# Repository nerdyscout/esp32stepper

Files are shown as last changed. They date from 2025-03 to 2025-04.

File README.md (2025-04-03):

# ESP32STEPPER

current state: untested :warning:

inspired by [joshr120/PD-Stepper](https://github.com/joshr120/PD-Stepper) but being fully open hardware/software.

Stepper motor controller using silent Trinamic TMC2209, ESP32-S3 and USB-PD mountable onto any NEMA17 motor. 

## Main Features:
- **TMC2209** stepper motor driver
- **ESP32-S3**
  - alternatively NE555 pulse generator
- **USB Power Delivery** providing up to 20V operation
  - alternatively external voltage supply possible
- **MPU-6050** 6axis accelerometer
- **BME280** temperature sensor
- **QWIIC** connector for external I2C components
- 2x **WS2812** RGB LEDs
- 2x **Push Buttons**
- optional 0.96" 128x96 **LC-Display**
- **JTAG** pins accessible
- **3 GPIO** pins and **UART** available

## PCB - License CERN-OHL-P-2.0

### Schematic

schematic

### Bill of Materials

The complete BOM is available in different formats:
  - raw [HTML](pcb/docs/bom/esp32stepper-bom.html)
  - interactive [HTML](nerdyscout.github.io/esp32stepper)
  - [CSV](pcb/docs/bom/esp32stepper-bom_octopart.csv) compliant to octopart

### Layout

| Top | Bottom |
| --- | --- |
| top view | bottom view |

### Gerbers

All fabrication files needed to produce this PCB are located within the [release package](https://github.com/nerdyscout/esp32stepper/releases).

## Mechanics

in the folder `cad` the spacers between motor and PCB, as well as the housing, can be found. One of the two spacer parts can be made out of metal to act as heatsink for the TMC2209. 

## Firmware

### ESPHome

There is a [esphome](https://esphome.io/) config file supporting different features located at `firmware/esphome`

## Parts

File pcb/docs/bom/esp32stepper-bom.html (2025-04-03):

Source File | esp32stepper.kicad_sch
BoM Date | Date
Schematic Version | 1.0
Schematic Date | 2025-03-16
PCB Variant | default
KiCad Version | Eeschema 9.0.1
Component Groups | 51
Component Count (per PCB) | 80
Fitted Components (per PCB) | 65
Number of PCBs | 1
Total Component Count (for 1 PCBs) | 65
 | Description | Part | References | Value | Footprint | Quantity Per PCB | Datasheet | variant | lcsc | sim.device | sim.pins | prod_id
1 | Unpolarized capacitor | C | C8C17C20C21C22C24 | 100nF | C_0402_1005Metric_Pad0.74x0.62mm_HandSolder | 6 | ~ | MPU | C7432762
2 | Unpolarized capacitor | C | C2C4C11C19 | 1µF | C_0402_1005Metric_Pad0.74x0.62mm_HandSolder | 4 | ~ | ESP32 USBPD | C14445
3 | Unpolarized capacitor | C | C14C15 | 10µF | C_0402_1005Metric_Pad0.74x0.62mm_HandSolder | 2 | ~ |  | C5252392
4 | Unpolarized capacitor | C | C3 | 10uF | C_0603_1608Metric_Pad1.08x0.95mm_HandSolder | 1 | ~ |  | C22367827
5 | Unpolarized capacitor | C | C13 | 100nF 16V | C_0402_1005Metric_Pad0.74x0.62mm_HandSolder | 1 | ~ |  | C7432762
6 | Unpolarized capacitor | C | C5C18 | 100nF 35V | C_0603_1608Metric_Pad1.08x0.95mm_HandSolder | 2 | ~ |  | C5342943
7 | Polarized capacitor | C_Polarized | C16 | 100µF 35V | C_Elec_6.3x7.7 | 1 | ~ |  | C4747966
8 | Unpolarized capacitor | C | C12 | 10µF 35V | C_0603_1608Metric_Pad1.08x0.95mm_HandSolder | 1 | ~ |  | C22367827
9 | Unpolarized capacitor | C | C7C9C10 | 1µF 35V | C_0603_1608Metric_Pad1.08x0.95mm_HandSolder | 3 | ~ |  | C7432774
10 | Unpolarized capacitor | C | C23 | 2,2nF 50V | C_0603_1608Metric_Pad1.08x0.95mm_HandSolder | 1 | ~ | MPU | C5119310
11 | Unpolarized capacitor | C | C6 | 22nF 50V | C_0603_1608Metric_Pad1.08x0.95mm_HandSolder | 1 | ~ |  | C915842
12 | Diode | D | D3 | D | D_SOD-123 | 1 | ~ | FAN | C95872 | D | 1=K 2=A
13 | RGB LED with integrated controller, 2.0 x 2.0 mm, 12 mA | WS2812B-2020 | D1D2 | WS2812B-2020 | LED_WS2812B-2020_PLCC4_2.0x2.0mm | 2 | https://cdn-shop.adafruit.com/product-files/4684/4684_WS2812B-2020_V1.3_EN.pdf | ESP32 | C965555
14 | Generic connector, single row, 01x07, script generated (kicad-library-utils/schlib/autogen/connector/) | Conn_01x07 | J1 | IO | JST_SH_SM07B-SRSS-TB_1x07-1MP_P1.00mm_Horizontal | 1 | https://www.jst-mfg.com/product/pdf/eng/eSH.pdf |  | C160406
15 | 4 pin JST 1mm polarized connector for I2C | Qwiic_Vertical | J4 | Qwiic_Vertical | JST_SH_SM04B-SRSS-TB_1x04-1MP_P1.00mm_Horizontal | 1 | https://www.jst-mfg.com/product/pdf/eng/eSH.pdf |  | C160404 |  |  | CONN-14483
16 | Generic connector, single row, 01x04, script generated (kicad-library-utils/schlib/autogen/connector/) | Conn_01x04 | J5 | Stepper | JST_PH_S4B-PH-K_1x04_P2.00mm_Horizontal | 1 | ~ |  | C19271361
17 | USB 2.0-only 14P Type-C Receptacle connector | USB_C_Receptacle_USB2.0_14P | J9 | USB_C_Receptacle_USB2.0_14P | USB_C_Receptacle_G-Switch_GT-USB-7010ASV | 1 | https://www.usb.org/sites/default/files/documents/usb_type-c.zip | USBPD | C2988369
18 | Inductor | L | L1 | 4,7µH | L_Bourns-SRN4018 | 1 | ~ |  | C1330726
19 | -3.6A Id, -30V Vds, 64mOhm Rds, P-Channel HEXFET Power MOSFET, SOT-23 | IRLML9301 | Q1Q2 | IRLML9301 | SOT-23 | 2 | https://www.infineon.com/dgdl/irlml9301pbf.pdf?fileId=5546d462533600a401535668e5e42640 | FAN | C7472922
20 | Resistor | R | R3R11 | 100m | R_0805_2012Metric_Pad1.20x1.40mm_HandSolder | 2 | ~ |  | C723643
21 | Resistor | R | R14 | 30 | R_0402_1005Metric_Pad0.72x0.64mm_HandSolder | 1 | ~ |  | C965208
22 | Resistor | R | R18 | 1k | R_0402_1005Metric_Pad0.72x0.64mm_HandSolder | 1 | ~ | USBPD | C2077651
23 | Resistor | R | R5 | 2k7 | R_0402_1005Metric_Pad0.72x0.64mm_HandSolder | 1 | ~ | ESP32 | C203149
24 | Resistor | R | R1R12R21 | 4k7 | R_0402_1005Metric_Pad0.72x0.64mm_HandSolder | 3 | ~ | ESP32 | C159885
25 | Resistor | R | R6R7R8R10R13R15R16R17R20R26 | 10k | R_0402_1005Metric_Pad0.72x0.64mm_HandSolder | 10 | ~ | ESP32 USBPD FAN | C304153
26 | Resistor | R | R2R4 | 20k | R_0402_1005Metric_Pad0.72x0.64mm_HandSolder | 2 | ~ | ESP32 | C93942
27 | Resistor | R | R9 | 33k | R_0402_1005Metric_Pad0.72x0.64mm_HandSolder | 1 | ~ |  | C427218
28 | Potentiometer | R_Potentiometer | RV1 | Potentiometer | Potentiometer_Bourns_TC33X_Vertical | 1 | ~ |  | C720648
29 | Microminiature SMT Side Actuated, 4.2 x 2.8 x 1.42mm, without pegs, with shield pin | CK_KMS2xxG | SW3 | B1 | SW_SPST_CK_KMS2xxGP | 1 | https://www.ckswitches.com/media/1482/kms.pdf | ESP32 | C221703
30 | Microminiature SMT Side Actuated, 4.2 x 2.8 x 1.42mm, without pegs, with shield pin | CK_KMS2xxG | SW4 | B2 | SW_SPST_CK_KMS2xxGP | 1 | https://www.ckswitches.com/media/1482/kms.pdf | ESP32 | C221703
31 | Microminiature SMT Side Actuated, 4.2 x 2.8 x 1.42mm, without pegs, with shield pin | CK_KMS2xxG | SW1 | BOOT | SW_SPST_CK_KMS2xxGP | 1 | https://www.ckswitches.com/media/1482/kms.pdf | ESP32 | C221703
32 | Microminiature SMT Side Actuated, 4.2 x 2.8 x 1.42mm, without pegs, with shield pin | CK_KMS2xxG | SW2 | RST | SW_SPST_CK_KMS2xxGP | 1 | https://www.ckswitches.com/media/1482/kms.pdf | ESP32 | C221703
33 | 3-in-1 sensor, humidity, pressure, temperature, I2C and SPI interface, 1.71-3.6V, LGA-8 | BME280 | U3 | BME280 | Bosch_LGA-8_2.5x2.5mm_P0.65mm_ClockwisePinNumbering | 1 | https://www.bosch-sensortec.com/media/boschsensortec/downloads/datasheets/bst-bme280-ds002.pdf | ESP32 | C92489
34 | 100W USB Type-C PD3.0/2.0, BC1.2 Sink Controller, SSOP-10 | CH224K | U6 | CH224K | SSOP-10-1EP_3.9x4.9mm_P1mm_EP2.1x3.3mm | 1 | https://www.wch.cn/downloads/file/301.html | USB | C970725
35 | Smallsized module supporting 2.4 GHz WiFi (802.11 b/g/n) and Bluetooth ® 5 (LE) Built around ESP32S3 series of SoCs, Xtensa ® dualcore 32bit LX7 microprocessor Flash up to 8 MB, optional 2 MB PSRAM in chip package 39 GPIOs, rich set of peripherals Onboard PCB antenna or external antenna connector | ESP32-S3-MINI-1 | U4 | ESP32-S3-MINI-1 | ESP32-S3-MINI-1 | 1 | https://www.espressif.com/sites/default/files/documentation/esp32-s3-mini-1_mini-1u_datasheet_en.pdf | ESP32 | C2913206
36 | InvenSense 6-Axis Motion Sensor, Gyroscope, Accelerometer, I2C | MPU-6050 | U7 | MPU-6050 | InvenSense_QFN-24_4x4mm_P0.5mm | 1 | https://invensense.tdk.com/wp-content/uploads/2015/02/MPU-6000-Datasheet1.pdf | MPU | C24112
37 | Standalone driver for two-phase bipolar stepper motor, 2A, 4.75… 36V, UART, internal FETs, QFN28 | TMC2208-LA | U2 | TMC2208-LA | QFN-28-1EP_5x5mm_P0.5mm_EP3.1x3.1mm_ThermalVias | 1 | https://www.analog.com/media/en/technical-documentation/data-sheets/TMC2202_TMC2208_TMC2224_datasheet_rev1.13.pdf |  | C115944
38 | 4.5V to 24V Input, 3-A Output Synchronous Buck Converter, SOT-23-6 | TPS56339DDC | U5 | TPS56339DDC | SOT-23-6 | 1 | https://www.ti.com/lit/ds/symlink/tps56339.pdf |  | C2071106
 | Description | Part | References | Value | Footprint | Quantity Per PCB | Datasheet | variant | lcsc | sim.device | sim.pins | prod_id
1 | Unpolarized capacitor | C | C1 | 100nF | C_0402_1005Metric_Pad0.74x0.62mm_HandSolder | 1 (DNF) | ~ | NE555
2 | Unpolarized capacitor | C | C25 | 1µF | C_0603_1608Metric_Pad1.08x0.95mm_HandSolder | 1 (DNF) | ~ | NE555
3 | Generic connector, single row, 01x04, script generated (kicad-library-utils/schlib/autogen/connector/) | Conn_01x04 | J3 | Display 0.96" 128x96 | PinSocket_1x04_P2.54mm_Vertical | 1 (DNF) | ~
4 | Generic connector, single row, 01x03, script generated (kicad-library-utils/schlib/autogen/connector/) | Conn_01x03 | J8 | FAN | Harwin_M20-89003xx_1x03_P2.54mm_Horizontal | 1 (DNF) | ~
5 | Cortex Debug Connector, standard ARM Cortex-M SWD and JTAG interface | Conn_ARM_JTAG_SWD_10 | J7 | JTAG | PinHeader_2x05_P1.27mm_Vertical_SMD | 1 (DNF) | http://infocenter.arm.com/help/topic/com.arm.doc.ddi0314h/DDI0314H_coresight_components_trm.pdf
6 | 2 Pin 2mm JST Battery Connector | Conn_01x02_JST_2.0mm_LiPo | J6 | PWR | JST_SMD_2.0mm-2 | 1 (DNF) | ~ |  |  |  |  | CONN-11443
7 | Solder Jumper, 2-pole, open | SolderJumper_2_Open | JP3 | MS1 | SolderJumper-2_P1.3mm_Open_RoundedPad1.0x1.5mm | 1 (DNF) | ~
8 | Solder Jumper, 2-pole, open | SolderJumper_2_Open | JP4 | MS2 | SolderJumper-2_P1.3mm_Open_RoundedPad1.0x1.5mm | 1 (DNF) | ~
9 | Resistor | R | R24 | 1k | R_0402_1005Metric_Pad0.72x0.64mm_HandSolder | 1 (DNF) | ~ | NE555
10 | Resistor | R | R19R22R25 | 10k | R_0402_1005Metric_Pad0.72x0.64mm_HandSolder | 3 (DNF) | ~ | USBPD NE555 | C304153
11 | Resistor | R | R23 | 20k | R_0402_1005Metric_Pad0.72x0.64mm_HandSolder | 1 (DNF) | ~ | NE555
12 | Rotary encoder, dual channel, incremental quadrate outputs | RotaryEncoder | SW5 | RotaryEncoder |  | 1 (DNF) | ~
13 | Precision Timers, 555 compatible, VSSOP-8 | LM555xMM | U1 | LM555xMM | VSSOP-8_3x3mm_P0.65mm | 1 (DNF) | http://www.ti.com/lit/ds/symlink/lm555.pdf | NE555

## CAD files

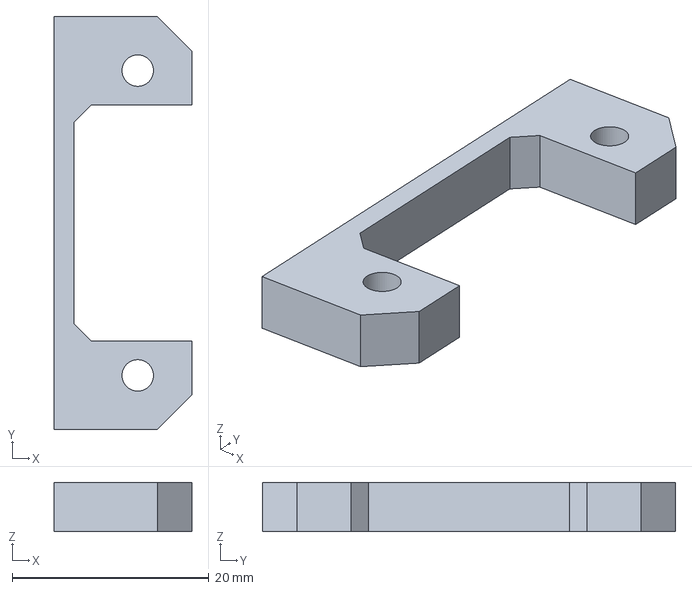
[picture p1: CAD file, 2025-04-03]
cad/plastic.step
14.0 x 42.0 x 5.00 mm

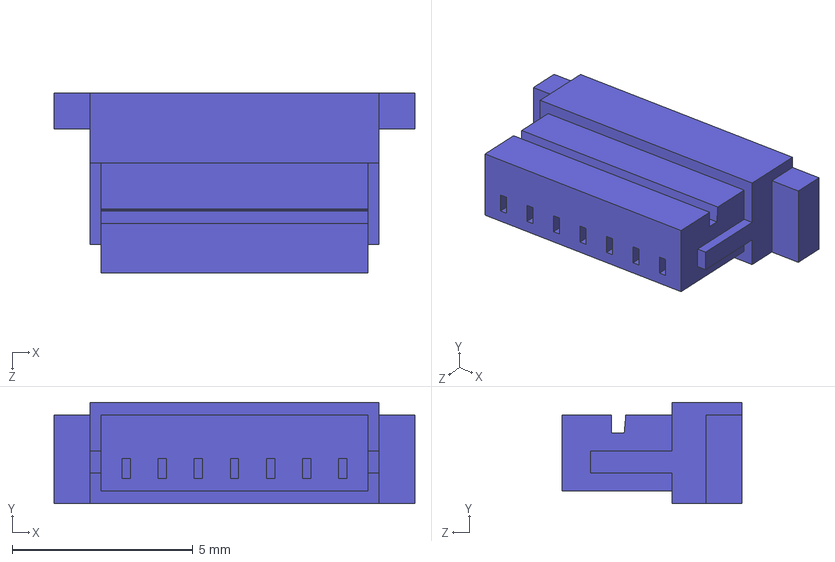
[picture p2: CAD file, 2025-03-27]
pcb/3dmodels/SHR-07V-S-B.step
10.0 x 2.80 x 5.00 mm

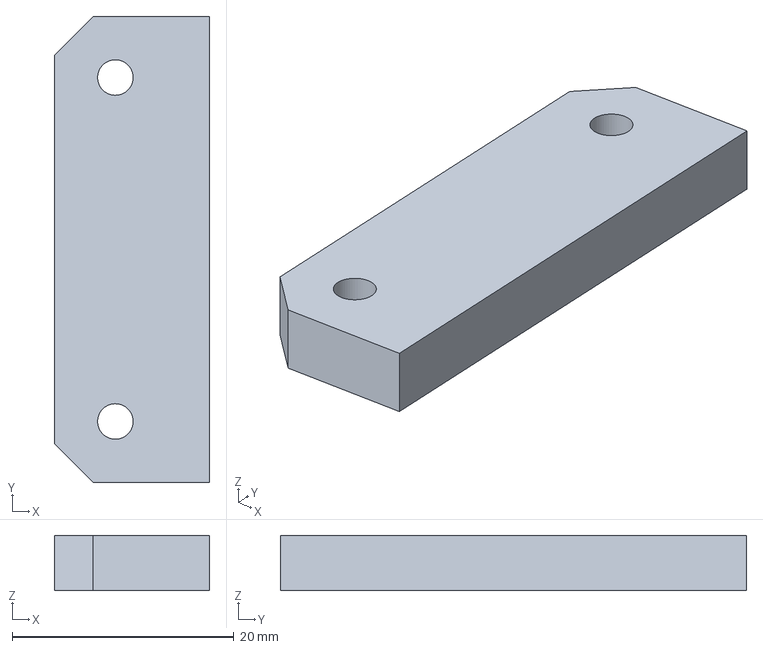
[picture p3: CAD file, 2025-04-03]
cad/metal.step
14.0 x 42.0 x 5.00 mm

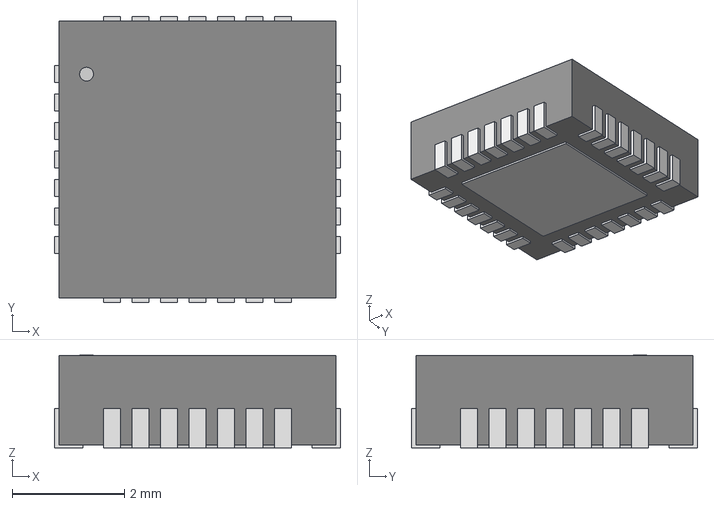
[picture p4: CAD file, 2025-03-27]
pcb/3dmodels/QFN28_5X5MC_MCH.step
5.11 x 5.11 x 1.65 mm

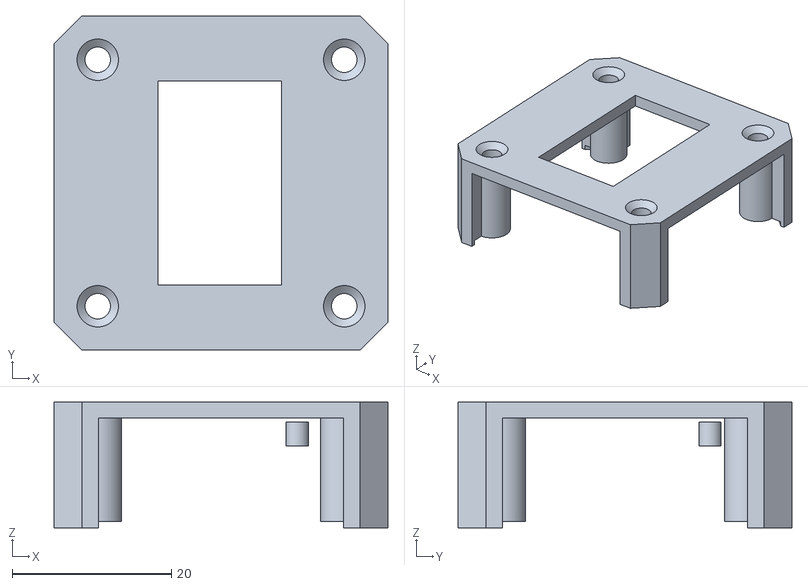
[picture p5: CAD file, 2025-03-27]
cad/cover_with_lcd.stl
42.0 x 42.0 x 15.8

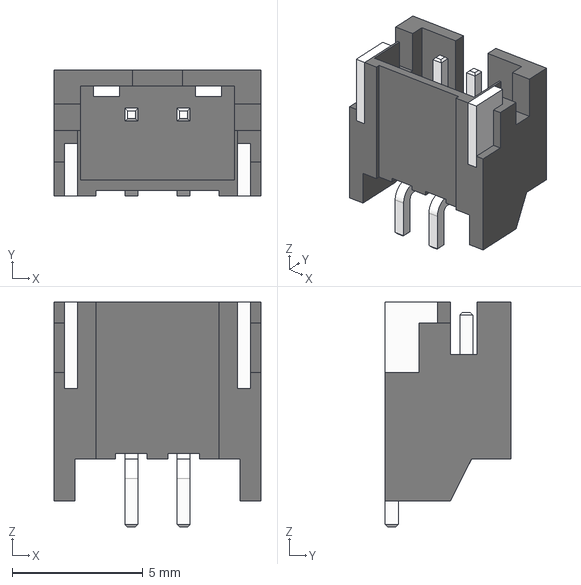
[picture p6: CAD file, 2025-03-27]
pcb/3dmodels/JST-PH-2 v1.step
7.90 x 4.80 x 8.60 mm

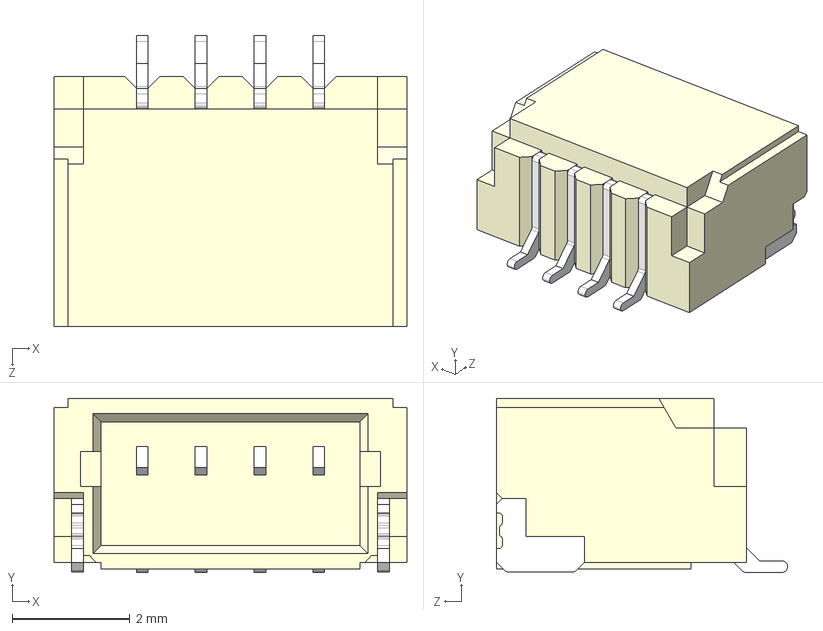
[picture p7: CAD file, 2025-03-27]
pcb/3dmodels/SM04B-SRSS-TB.step
6.00 x 2.96 x 4.95 mm

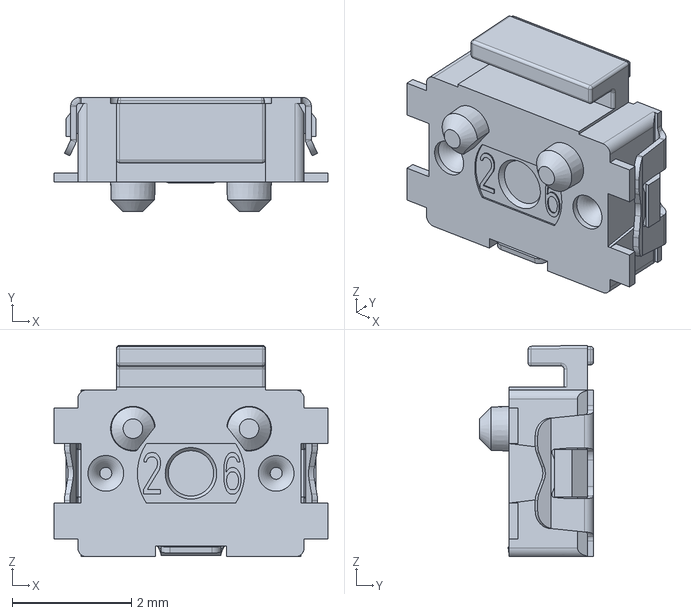
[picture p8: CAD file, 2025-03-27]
pcb/3dmodels/KMS221GPLFS.step
4.60 x 1.92 x 3.55 mm

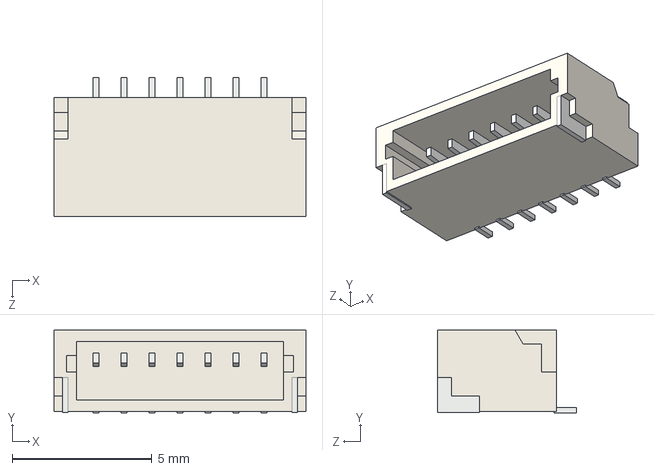
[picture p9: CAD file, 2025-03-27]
pcb/3dmodels/JST SM07B-SRSS-TB.step
9.00 x 2.96 x 4.95 mm

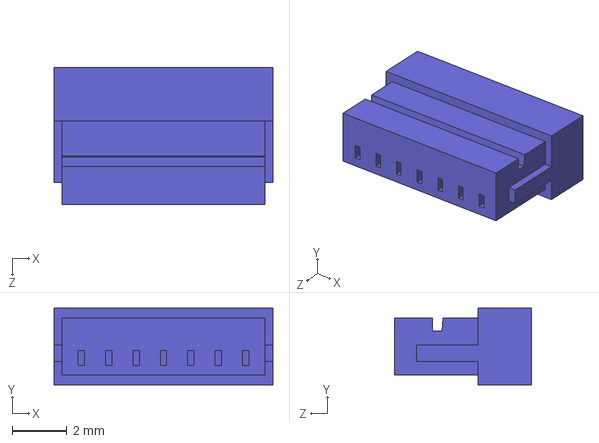
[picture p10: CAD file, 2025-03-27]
pcb/3dmodels/SHR-07V-S.step
8.00 x 2.80 x 5.00 mm

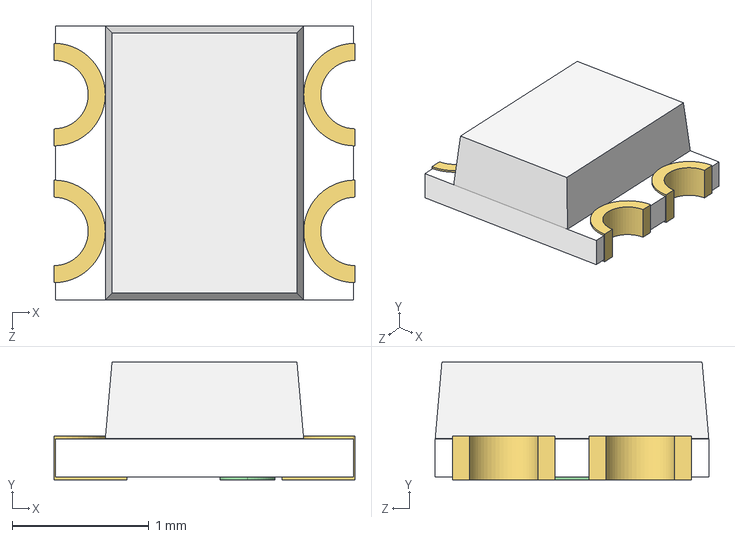
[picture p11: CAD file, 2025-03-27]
pcb/3dmodels/WS2812-2020.step
2.20 x 0.86 x 2.00 mm

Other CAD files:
cad/metal.stl
cad/plastic.stl

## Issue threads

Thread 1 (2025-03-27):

tasks left to do

nerdyscout, 2025-03-27:
* [ ] add option to use AS5600
 * [ ] check if magnetic sensor can detect rotation, distance piece might be to tall
 * [ ] improve documentation
 * [ ] make sure pnp file fits jlcpcb
 * [ ] add OSHWA id to pcb once granted

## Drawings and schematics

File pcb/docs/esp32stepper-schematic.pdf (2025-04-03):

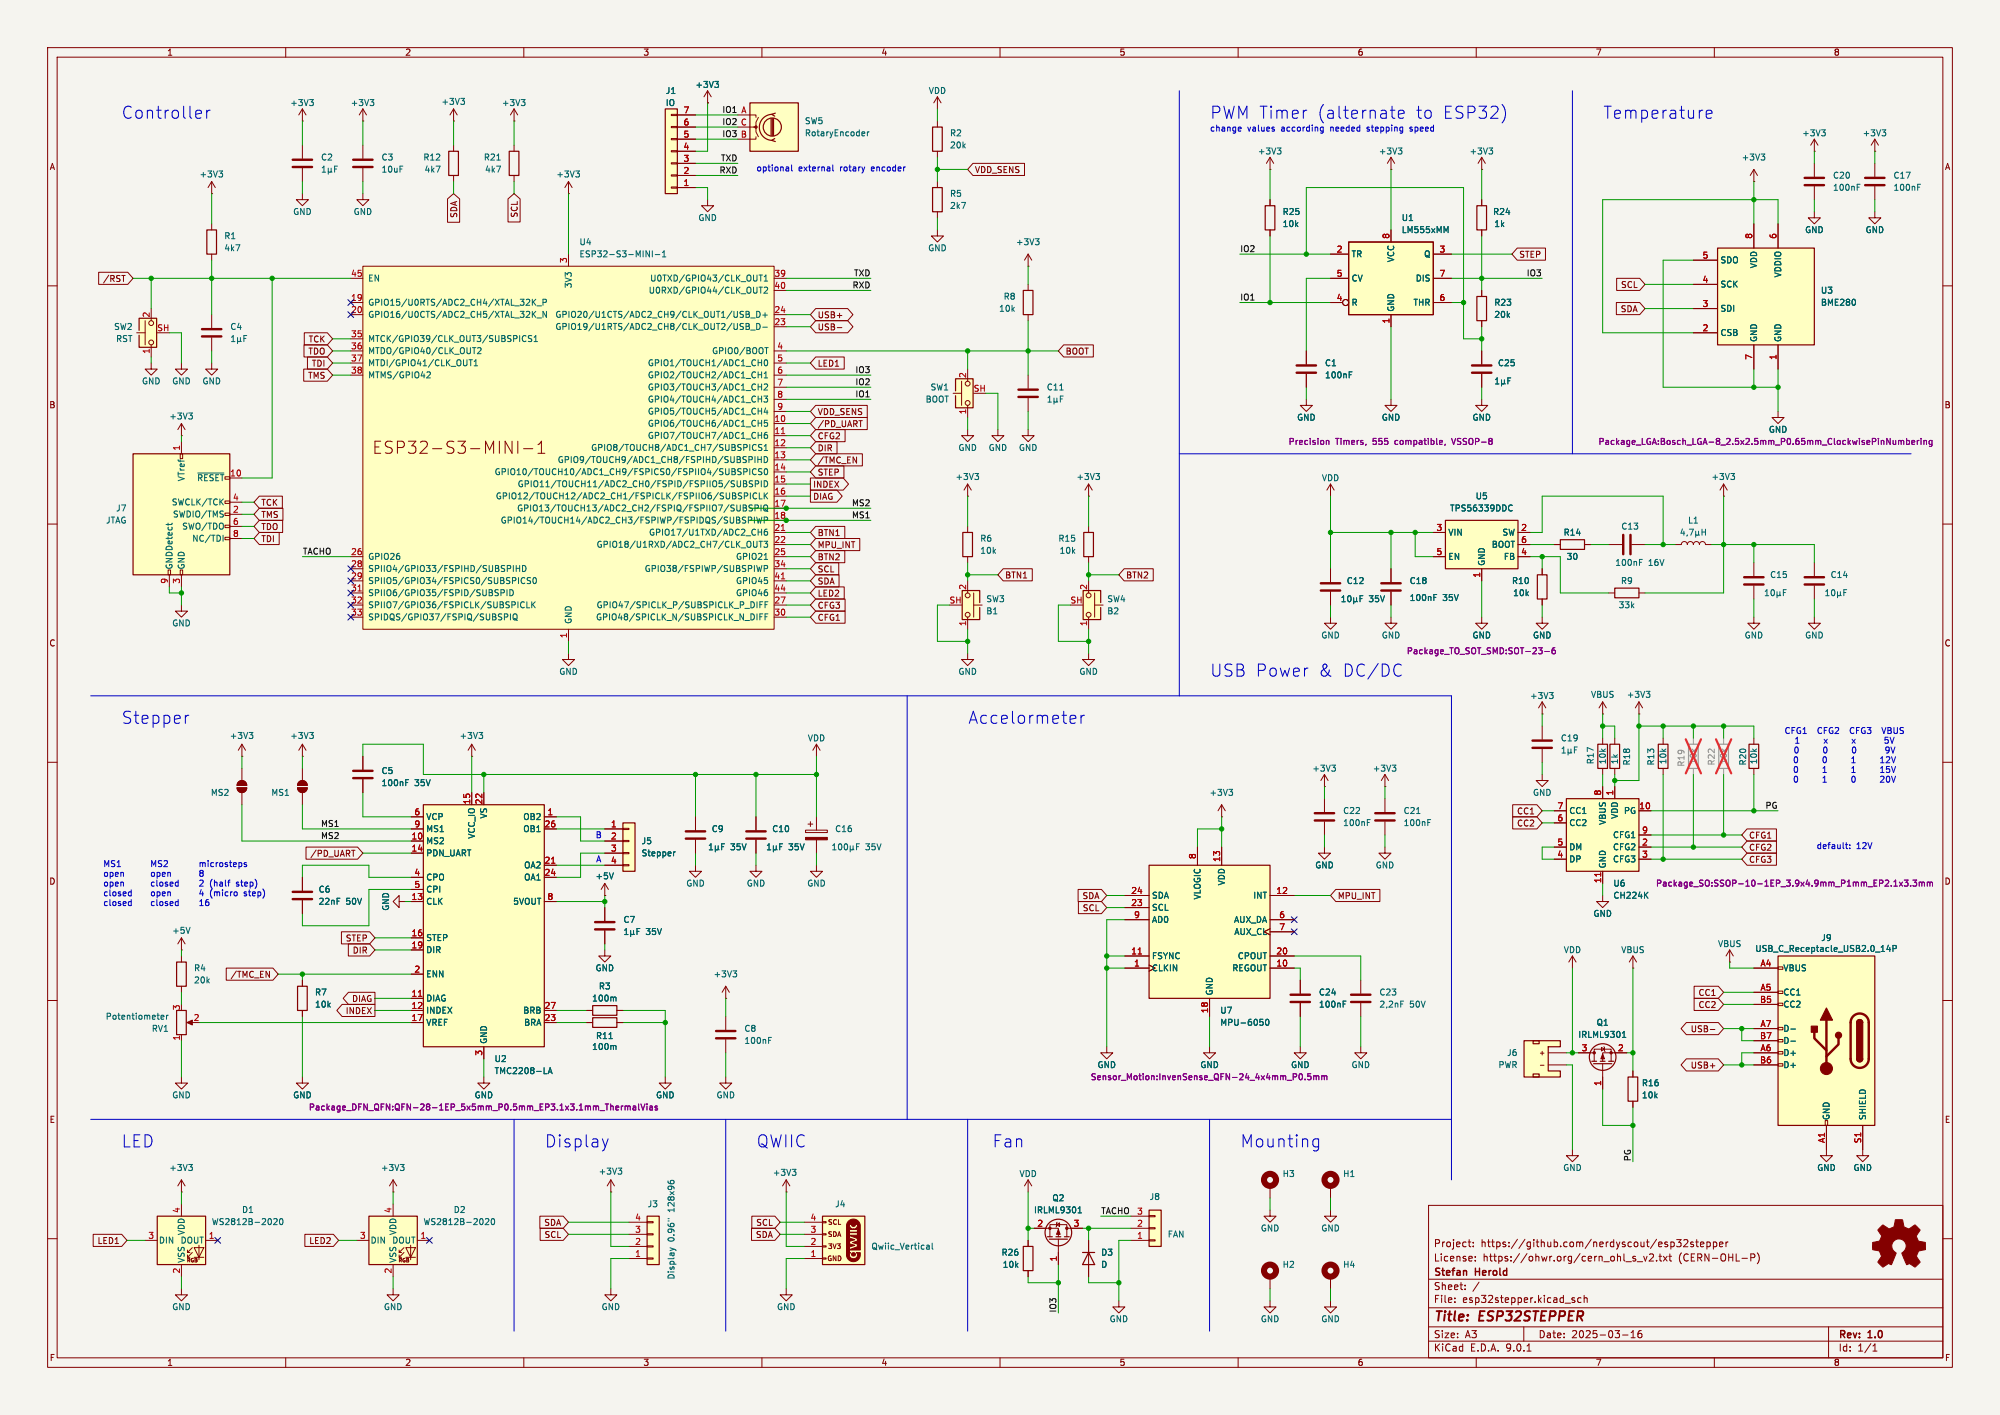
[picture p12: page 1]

1 U0TXD/GPIO43/CLK_OUT1 39 U0RXD/GPIO44/CLK_OUT2 40 GPIO20/U1CTS/ADC2_CH9/CLK_OUT1/USB_D+ 24 GPIO19/U1RTS/ADC2_CH8/CLK_OUT2/USB_D- 23 GPIO0/BOOT 4 GPIO1/TOUCH1/ADC1_CH0 5 GPIO2/TOUCH2/ADC1_CH1 6 GPIO3/TOUCH3/ADC1_CH2 7 GPIO4/TOUCH4/ADC1_CH3 8 GPIO5/TOUCH5/ADC1_CH4 9 GPIO6/TOUCH6/ADC1_CH5 10 GPIO7/TOUCH7/ADC1_CH6 11 GPIO8/TOUCH8/ADC1_CH7/SUBSPICS1 12 GPIO9/TOUCH9/ADC1_CH8/FSPIHD/SUBSPIHD 13 GPIO10/TOUCH10/ADC1_CH9/FSPICS0/FSPIIO4/SUBSPICS0 14 GPIO11/TOUCH11/ADC2_CH0/FSPID/FSPIIO5/SUBSPID 15 GPIO12/TOUCH12/ADC2_CH1/FSPICLK/FSPIIO6/SUBSPICLK 16 GPIO13/TOUCH13/ADC2_CH2/FSPIQ/FSPIIO7/SUBSPIQ 17 GPIO14/TOUCH14/ADC2_CH3/FSPIWP/FSPIDQS/SUBSPIWP 18 GPIO17/U1TXD/ADC2_CH6 21 GPIO18/U1RXD/ADC2_CH7/CLK_OUT3 22 GPIO21 25 GPIO38/FSPIWP/SUBSPIWP 34 GPIO45 41 GPIO46 44 GPIO47/SPICLK_P/SUBSPICLK_P_DIFF 27 GPIO48/SPICLK_N/SUBSPICLK_N_DIFF 30 U4ESP32-S3-MINI-1 +3V3

þÿ1µF GND GND GND

3 ~{RESET}10 SWCLK/TCK 4 SWDIO/TMS 2 SWO/TDO 6 NC/TDI 8

VCP 6 MS1 9 MS2 10 PDN_UART 14 CPO 4 CPI 5 CLK 13 STEP 16 DIR 19 ENN 2 DIAG 11

USB Power & DC/DC

Package_DFN_QFN:QFN-28-1EP_5x5mm_P0.5mm_EP3.1x3.1mm_ThermalVias VCP 6 MS1 9 MS2 10 PDN_UART 14 CPO 4 CPI 5 CLK 13 STEP 16 DIR 19 ENN 2 DIAG 11

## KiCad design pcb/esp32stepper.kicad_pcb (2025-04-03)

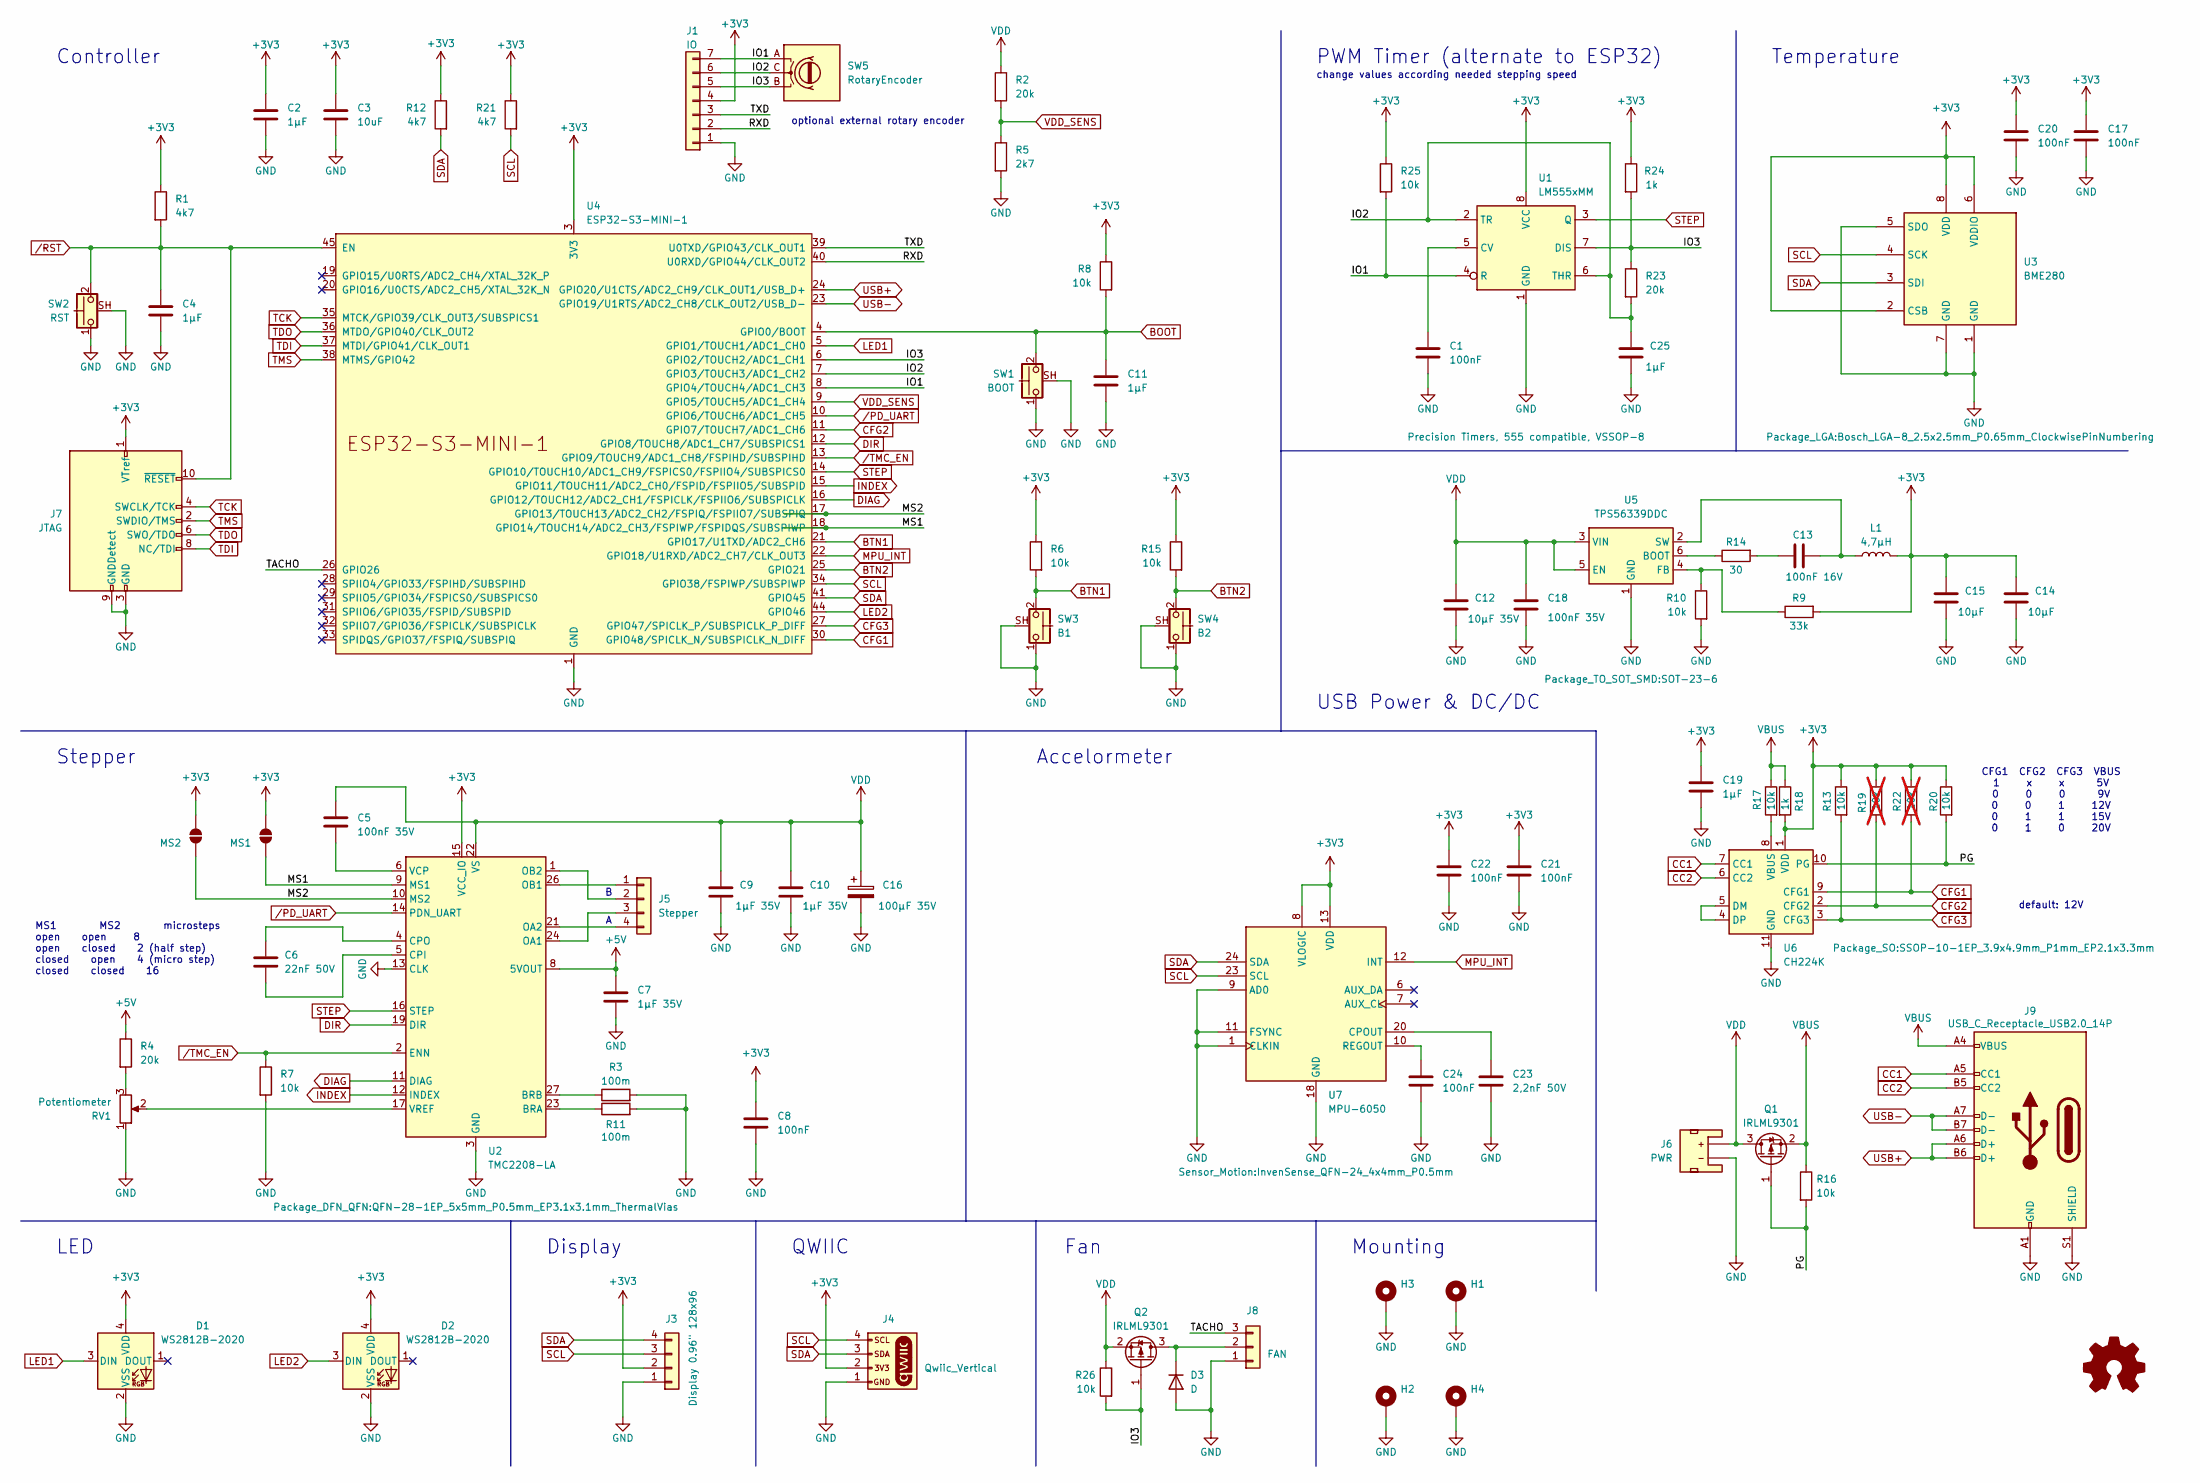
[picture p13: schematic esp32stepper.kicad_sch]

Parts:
C1: 100nF; C_0402_1005Metric_Pad0.74x0.62mm_HandSolder
C2, C4, C11, C19: 1µF; C_0402_1005Metric_Pad0.74x0.62mm_HandSolder; LCSC C14445
C3: 10uF; C_0603_1608Metric_Pad1.08x0.95mm_HandSolder; LCSC C22367827
C5, C18: 100nF 35V; C_0603_1608Metric_Pad1.08x0.95mm_HandSolder; LCSC C5342943
C6: 22nF 50V; C_0603_1608Metric_Pad1.08x0.95mm_HandSolder; LCSC C915842
C7, C9, C10: 1µF 35V; C_0603_1608Metric_Pad1.08x0.95mm_HandSolder; LCSC C7432774
C8, C17, C20, C21, C22, C24: 100nF; C_0402_1005Metric_Pad0.74x0.62mm_HandSolder; LCSC C7432762
C12: 10µF 35V; C_0603_1608Metric_Pad1.08x0.95mm_HandSolder; LCSC C22367827
C13: 100nF 16V; C_0402_1005Metric_Pad0.74x0.62mm_HandSolder; LCSC C7432762
C14, C15: 10µF; C_0402_1005Metric_Pad0.74x0.62mm_HandSolder; LCSC C5252392
C16: 100µF 35V; C_Elec_6.3x7.7; LCSC C4747966
C23: 2,2nF 50V; C_0603_1608Metric_Pad1.08x0.95mm_HandSolder; LCSC C5119310
C25: 1µF; C_0603_1608Metric_Pad1.08x0.95mm_HandSolder
D1, D2: WS2812B-2020; LED_WS2812B-2020_PLCC4_2.0x2.0mm; LCSC C965555
D3: D; D_SOD-123; LCSC C95872
H1, H2, H3, H4: MountingHole_Pad; MountingHole_3.2mm_M3_Pad_Via
J1: IO; JST_SH_SM07B-SRSS-TB_1x07-1MP_P1.00mm_Horizontal; LCSC C160406
J3: Display 0.96" 128x96; PinSocket_1x04_P2.54mm_Vertical
J4: Qwiic_Vertical; JST_SH_SM04B-SRSS-TB_1x04-1MP_P1.00mm_Horizontal; LCSC C160404
J5: Stepper; JST_PH_S4B-PH-K_1x04_P2.00mm_Horizontal; LCSC C19271361
J6: PWR; JST_SMD_2.0mm-2
J7: JTAG; PinHeader_2x05_P1.27mm_Vertical_SMD
J8: FAN; Harwin_M20-89003xx_1x03_P2.54mm_Horizontal
J9: USB_C_Receptacle_USB2.0_14P; USB_C_Receptacle_G-Switch_GT-USB-7010ASV; LCSC C2988369
JP3: MS1; SolderJumper-2_P1.3mm_Open_RoundedPad1.0x1.5mm
JP4: MS2; SolderJumper-2_P1.3mm_Open_RoundedPad1.0x1.5mm
L1: 4,7µH; L_Bourns-SRN4018; LCSC C1330726
Q1, Q2: IRLML9301; SOT-23; LCSC C7472922
R1, R12, R21: 4k7; R_0402_1005Metric_Pad0.72x0.64mm_HandSolder; LCSC C159885
R2, R4: 20k; R_0402_1005Metric_Pad0.72x0.64mm_HandSolder; LCSC C93942
R3, R11: 100m; R_0805_2012Metric_Pad1.20x1.40mm_HandSolder; LCSC C723643
R5: 2k7; R_0402_1005Metric_Pad0.72x0.64mm_HandSolder; LCSC C203149
R6, R7, R8, R10, R13, R15, R16, R17, R20, R26: 10k; R_0402_1005Metric_Pad0.72x0.64mm_HandSolder; LCSC C304153
R9: 33k; R_0402_1005Metric_Pad0.72x0.64mm_HandSolder; LCSC C427218
R14: 30; R_0402_1005Metric_Pad0.72x0.64mm_HandSolder; LCSC C965208
R18: 1k; R_0402_1005Metric_Pad0.72x0.64mm_HandSolder; LCSC C2077651
R19, R22: 10k; R_0402_1005Metric_Pad0.72x0.64mm_HandSolder; LCSC C304153; not fitted
R23: 20k; R_0402_1005Metric_Pad0.72x0.64mm_HandSolder
R24: 1k; R_0402_1005Metric_Pad0.72x0.64mm_HandSolder
R25: 10k; R_0402_1005Metric_Pad0.72x0.64mm_HandSolder
RV1: Potentiometer; Potentiometer_Bourns_TC33X_Vertical; LCSC C720648
SW1: BOOT; SW_SPST_CK_KMS2xxGP; LCSC C221703
SW2: RST; SW_SPST_CK_KMS2xxGP; LCSC C221703
SW3: B1; SW_SPST_CK_KMS2xxGP; LCSC C221703
SW4: B2; SW_SPST_CK_KMS2xxGP; LCSC C221703
SW5: RotaryEncoder
U1: LM555xMM; VSSOP-8_3x3mm_P0.65mm
U2: TMC2208-LA; QFN-28-1EP_5x5mm_P0.5mm_EP3.1x3.1mm_ThermalVias; LCSC C115944
U3: BME280; Bosch_LGA-8_2.5x2.5mm_P0.65mm_ClockwisePinNumbering; LCSC C92489
U4: ESP32-S3-MINI-1; LCSC C2913206
U5: TPS56339DDC; SOT-23-6; LCSC C2071106
U6: CH224K; SSOP-10-1EP_3.9x4.9mm_P1mm_EP2.1x3.3mm; LCSC C970725
U7: MPU-6050; InvenSense_QFN-24_4x4mm_P0.5mm; LCSC C24112

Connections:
+3V3: C2.1, C3.1, C8.1, C14.1, C15.1, C17.1, C19.1, C20.1, C21.1, C22.1, D1.4 (VDD), D2.4 (VDD), J1.4, J3.2, J4.2, J7.1 (VTref), JP3.1 (A), JP4.1 (A), L1.2, R1.1, R6.1, R8.1, R9.2, R12.1, R13.1, R15.1, R18.2, R19.1, R20.1, R21.1, R22.1, R24.1, R25.1, U1.8 (VCC), U2.15 (VCC_IO), U3.2 (CSB), U3.6 (VDDIO), U3.8 (VDD), U4.3 (3V3), U6.1 (VDD), U7.8 (VLOGIC), U7.13 (VDD)
+5V: C7.1, R4.1, U2.8 (5VOUT)
/IO1: J1.7, R25.2, SW5.A, U1.4 (R), U4.8 (GPIO4/TOUCH4/ADC1_CH3)
/IO2: C25.1, J1.6, R23.2, SW5.C, U1.2 (TR), U1.6 (THR), U4.7 (GPIO3/TOUCH3/ADC1_CH2)
/IO3: J1.5, Q2.1 (G), R23.1, R24.2, R26.2, SW5.B, U1.7 (DIS), U4.6 (GPIO2/TOUCH2/ADC1_CH1)
/MS1: JP3.2 (B), U2.9 (MS1), U4.18 (GPIO14/TOUCH14/ADC2_CH3/FSPIWP/FSPIDQS/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)
/MS2: JP4.2 (B), U2.10 (MS2), U4.17 (GPIO13/TOUCH13/ADC2_CH2/FSPIQ/FSPIIO7/S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)
/PG: Q1.1 (G), R16.2, R20.2, U6.10 (PG)
/RXD: J1.2, U4.40 (U0RXD/GPIO44/CLK_OUT2)
/TACHO: J8.3, U4.26 (GPIO26)
/TXD: J1.3, U4.39 (U0TXD/GPIO43/CLK_OUT1)
BOOT: C11.1, R8.2, SW1.2, U4.4 (GPIO0/BOOT)
BTN1: R6.2, SW3.2, U4.21 (GPIO17/U1TXD/ADC2_CH6)
BTN2: R15.2, SW4.2, U4.25 (GPIO21)
CC1: J9.A5 (CC1), U6.7 (CC1)
CC2: J9.B5 (CC2), U6.6 (CC2)
CFG1: R22.2, U4.30 (GPIO48/SPICLK_N/SUBSPICLK_N_DIFF), U6.9 (CFG1)
CFG2: R19.2, U4.11 (GPIO7/TOUCH7/ADC1_CH6), U6.2 (CFG2)
CFG3: R13.2, U4.27 (GPIO47/SPICLK_P/SUBSPICLK_P_DIFF), U6.3 (CFG3)
DIAG: U2.11 (DIAG), U4.16 (GPIO12/TOUCH12/ADC2_CH1/FSPICLK/FSPIIO6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)
DIR: U2.19 (DIR), U4.12 (GPIO8/TOUCH8/ADC1_CH7/SUBSPICS1)
GND: C1.2, C2.2, C3.2, C4.2, C7.2, C8.2, C9.2, C10.2, C11.2, C12.2, C14.2, C15.2, C16.2, C17.2, C18.2, C19.2, C20.2, C21.2, C22.2, C23.2, C24.2, C25.2, D1.2 (VSS), D2.2 (VSS), D3.2 (A), H1.1, H2.1, H3.1, H4.1, J1.1, J3.1, J4.1, J6.1 (-), J7.3 (GND), J7.5 (GND), J7.9 (GNDDetect), J8.1, J9.A1 (GND), J9.A12 (GND), J9.B1 (GND), J9.B12 (GND), J9.S1 (SHIELD), R3.2, R5.2, R7.2, R10.2, R11.2, RV1.1, SW1.1, SW1.SH (B), SW2.1, SW2.SH (B), SW3.1, SW3.SH (B), SW4.1, SW4.SH (B), U1.1 (GND), U2.3 (GND), U2.13 (CLK), U2.18 (GND), U2.29 (GND), U3.1 (GND), U3.5 (SDO), U3.7 (GND), U4.1 (GND), U4.2 (GND), U4.42 (GND), U4.43 (GND), U4.46 (GND), U4.47 (GND), U4.48 (GND), U4.49 (GND), U4.50 (GND), U4.51 (GND), U4.52 (GND), U4.53 (GND), U4.54 (GND), U4.55 (GND), U4.56 (GND), U4.57 (GND), U4.58 (GND), U4.59 (GND), U4.60 (GND), U4.61 (GND), U4.62 (GND), U4.63 (GND), U4.64 (GND), U4.65 (GND), U5.1 (GND), U6.11 (GND), U7.1 (CLKIN), U7.9 (AD0), U7.11 (FSYNC), U7.18 (GND)
INDEX: U2.12 (INDEX), U4.15 (GPIO11/TOUCH11/ADC2_CH0/FSPID/FSPIIO5/S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)
LED1: D1.3 (DIN), U4.5 (GPIO1/TOUCH1/ADC1_CH0)
LED2: D2.3 (DIN), U4.44 (GPIO46)
MPU_INT: U4.22 (GPIO18/U1RXD/ADC2_CH7/CLK_OUT3), U7.12 (INT)
unnamed: C13.1, R14.2
unnamed: D3.1 (K), J8.2, Q2.3 (D)
unnamed: J5.1, U2.26 (OB1)
unnamed: J5.2, U2.1 (OB2)
unnamed: J5.3, U2.24 (OA1)
unnamed: J5.4, U2.21 (OA2)
unnamed: R4.2, RV1.3
unnamed: C1.1, U1.5 (CV)
unnamed: R11.1, U2.23 (BRA)
unnamed: R3.1, U2.27 (BRB)
unnamed: C6.2, U2.5 (CPI)
unnamed: C6.1, U2.4 (CPO)
unnamed: C5.2, U2.6 (VCP)
unnamed: RV1.2, U2.17 (VREF)
unnamed: R14.1, U5.6 (BOOT)
unnamed: R9.1, R10.1, U5.4 (FB)
unnamed: C13.2, L1.1, U5.2 (SW)
unnamed: U6.4 (DP), U6.5 (DM)
unnamed: R17.2, U6.8 (VBUS)
unnamed: C23.1, U7.20 (CPOUT)
unnamed: C24.1, U7.10 (REGOUT)
SCL: J3.3, J4.4, R21.2, U3.4 (SCK), U4.34 (GPIO38/FSPIWP/SUBSPIWP), U7.23 (SCL)
SDA: J3.4, J4.3, R12.2, U3.3 (SDI), U4.41 (GPIO45), U7.24 (SDA)
STEP: U1.3 (Q), U2.16 (STEP), U4.14 (GPIO10/TOUCH10/ADC1_CH9/FSPICS0/FSPIIO4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)
TCK: J7.4 (SWCLK/TCK), U4.35 (MTCK/GPIO39/CLK_OUT3/SUBSPICS1)
TDI: J7.8 (NC/TDI), U4.37 (MTDI/GPIO41/CLK_OUT1)
TDO: J7.6 (SWO/TDO), U4.36 (MTDO/GPIO40/CLK_OUT2)
TMS: J7.2 (SWDIO/TMS), U4.38 (MTMS/GPIO42)
USB+: J9.A6 (D+), J9.B6 (D+), U4.24 (GPIO20/U1CTS/ADC2_CH9/CLK_OUT1/USB_D+)
USB-: J9.A7 (D-), J9.B7 (D-), U4.23 (GPIO19/U1RTS/ADC2_CH8/CLK_OUT2/USB_D-)
VBUS: J9.A4 (VBUS), J9.A9 (VBUS), J9.B4 (VBUS), J9.B9 (VBUS), Q1.2 (S), R16.1, R17.1, R18.1
VDD: C5.1, C9.1, C10.1, C12.1, C16.1, C18.1, J6.2 (+), Q1.3 (D), Q2.2 (S), R2.1, R26.1, U2.22 (VS), U2.28 (VS), U5.3 (VIN), U5.5 (EN)
VDD_SENS: R2.2, R5.1, U4.9 (GPIO5/TOUCH5/ADC1_CH4)
/PD_UART: U2.14 (PDN_UART), U4.10 (GPIO6/TOUCH6/ADC1_CH5)
/RST: C4.1, J7.10 (~RESET), R1.2, SW2.2, U4.45 (EN)
/TMC_EN: R7.1, U2.2 (ENN), U4.13 (GPIO9/TOUCH9/ADC1_CH8/FSPIHD/SUBSPIHD)

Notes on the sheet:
Mounting
LED
Accelormeter
Display
default: 12V
Temperature
CFG1 CFG2 CFG3 VBUS 1 x x 5V 0 0 0 9V 0 0 1 12V 0 1 1 15V 0 1 0 20V
optional external rotary encoder
Stepper
USB Power & DC/DC
QWIIC
Controller
MS1 MS2 microsteps open open 8 open closed 2 (half step) closed open 4 (micro step) closed closed 16
Fan
PWM Timer (alternate to ESP32)
change values according needed stepping speed

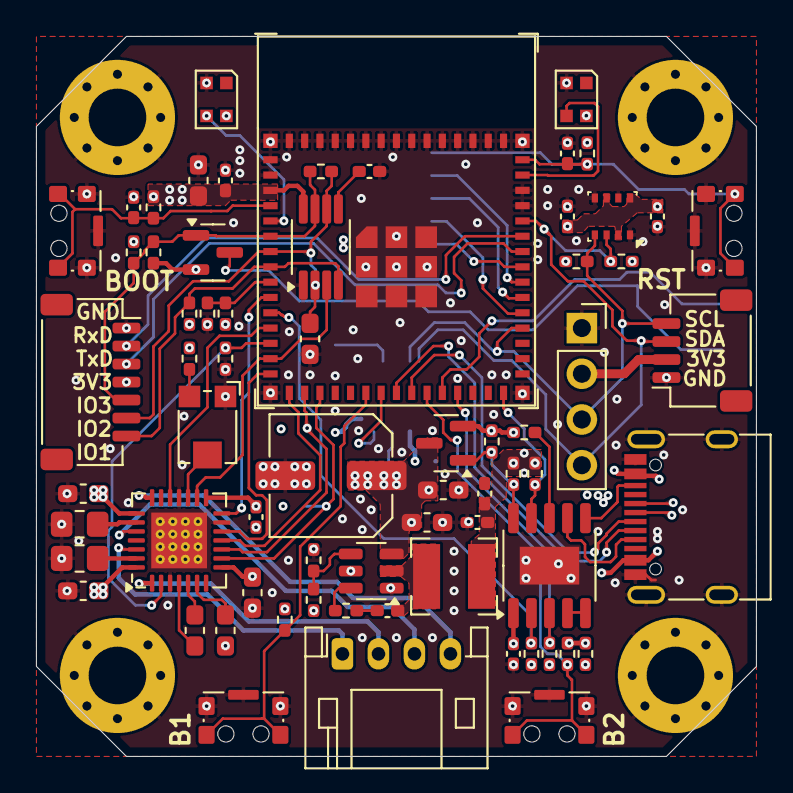
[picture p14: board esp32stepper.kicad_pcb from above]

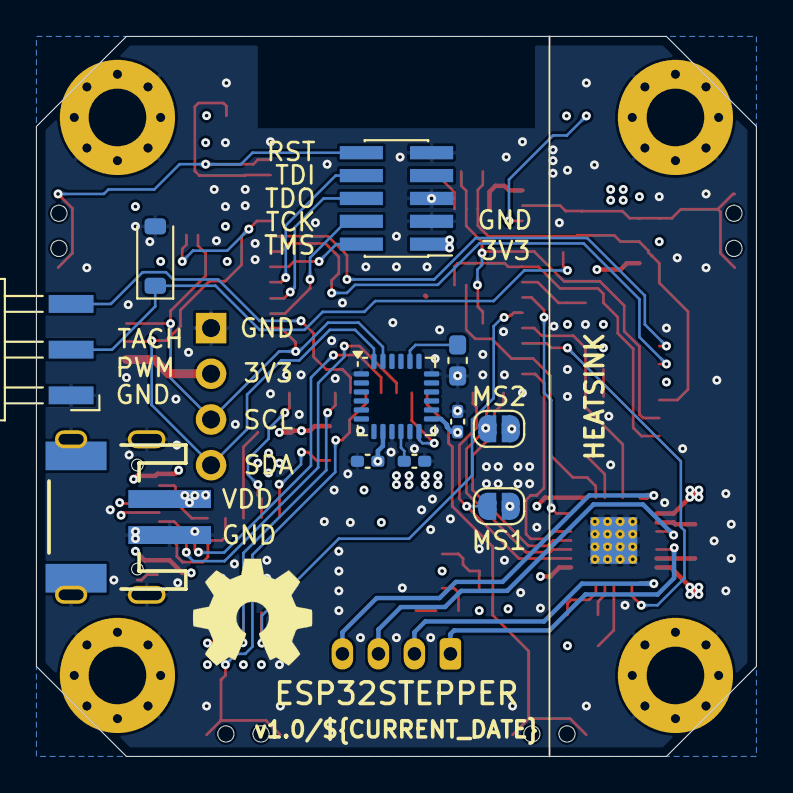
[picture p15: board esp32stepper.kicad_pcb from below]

Board: 4 copper layers, 40.0 x 40.0 mm, 83 parts (11 on the bottom side), 62 nets.

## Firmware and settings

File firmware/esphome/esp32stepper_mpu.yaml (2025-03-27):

# This example uses a custom TMC2209 component to control the PD Stepper
# Motor can be moved using a slider within ESPHome

external_components:
  - source: github://slimcdk/esphome-custom-components
    components: [tmc2209_hub, tmc2209, stepper]

esphome:
  #  name: esp32stepper
  project:
    name: esp32stepper
    version: "1.0"
  platformio_options:
    board_build.flash_mode: dio
    upload_speed: 921600
  on_boot:
    - tmc2209.configure:
        microsteps: 4
        direction: clockwise
        interpolation: true
        tcool_threshold: 400
    - tmc2209.stallguard:
        threshold: 60
    - tmc2209.currents:
        irun: 16
        ihold: 0
        tpowerdown: 0
        iholddelay: 0
        standstill_mode: freewheeling

    - output.turn_off: #Microstep resolution configuration (internal pull-down resistors: MS2, MS1: 00: 1/8, 01: 1/32, 10: 1/64 11: 1/16
        id: MS1_pin
    - output.turn_off:
        id: MS2_pin

      #set PD voltage    # 5V  9V  12V  15V  20V
    - output.turn_off: # 1   0    0    0    0
        id: CFG1_pin
    - output.turn_on: # -   0    0    1    1
        id: CFG2_pin
    - output.turn_off: # -   0    1    1    0
        id: CFG3_pin

esp32:
  board: esp32-s3-devkitc-1
  framework:
    type: arduino

# This should point to the public location of this yaml file.
dashboard_import:
  package_import_url: https://github.com/nerdyscout/esp32stepper/blob/main/software/esphome/esp32stepper.yaml
  import_full_config: false # or true

ota:
  platform: esphome
  password: !secret ota_password

wifi:
  ssid: !secret wifi_ssid
  password: !secret wifi_password

web_server:
  port: 80

captive_portal:

mqtt:
  broker: !secret mqtt_broker
  username: !secret mqtt_username
  password: !secret mqtt_password

api:
  password: !secret api_password

logger:

i2c:
  sda: GPIO45
  scl: GPIO38
  scan: true
#  id: bus_a

uart:
  tx_pin: GPIO43
  rx_pin: GPIO44
  baud_rate: 115200

output:
  - platform: gpio
    pin: GPIO14
    id: MS1_pin
  - platform: gpio
    pin: GPIO13
    id: MS2_pin

  - platform: gpio
    pin: GPIO48
    id: CFG1_pin
  - platform: gpio
    pin: GPIO07
    id: CFG2_pin
  - platform: gpio
    pin: GPIO47
    id: CFG3_pin

  - platform: gpio
    pin: GPIO04
    id: IO1
  - platform: gpio
    pin: GPIO03
    id: IO2
  - platform: gpio
    pin: GPIO02
    id: IO3

light:
  - platform: neopixelbus
    type: GRB
    variant: WS2811
    pin: GPIO01
    num_leds: 1
    id: led1
    name: "LED1"
  - platform: neopixelbus
    type: GRB
    variant: WS2811
    pin: GPIO46
    id: led2
    num_leds: 1
    name: "LED2"

stepper:
  - platform: tmc2209
    id: driver
    max_speed: 800 steps/s
    acceleration: 1500 steps/s^2
    deceleration: 1500 steps/s^2
    rsense: 100 mOhm
    vsense: False
    enn_pin: GPIO09
    diag_pin: GPIO12
    index_pin: GPIO11
    on_status:
      - logger.log:
          format: "Driver is reporting an update! (code %d)"
          args: ["code"]
    on_stall:
      - logger.log: "Motor stalled!"
      - stepper.stop: driver
      - light.turn_on:
          id: led1
          transition_length: 0s
      - delay: 250ms
      - light.turn_off:
          id: led1
          transition_length: 1s

button:
  - platform: restart
    name: Restart

  - platform: template
    name: Stop
    on_press:
      - stepper.stop: driver

binary_sensor:
  #  - platform: gpio
  #    name: "Power Good"
  #    pin:
  #      number: GPIO11
  #      mode: INPUT
  #      inverted: true
  #    device_class: power
  #    filters:
  #      - delayed_on: 10ms

  - platform: gpio
    name: Button 1
    pin:
      number: GPIO17
      mode: INPUT
      inverted: true
    id: btn1
    filters:
      - delayed_on: 10ms

  - platform: gpio
    name: Button 2
    id: btn2
    pin:
      number: GPIO21
      mode: INPUT
      inverted: true
    filters:
      - delayed_on: 10ms

display:
  - platform: ssd1306_i2c
    model: "SSD1306 128x64"
    lambda: |-
      it.print(0, 0, id(roboto), "Hello World!");

sensor:
  - platform: mpu6050
    #    address: 0x68
    update_interval: 0s
    accel_x:
      name: "MPU6050 Accel X"
    accel_y:
      name: "MPU6050 Accel Y"
    accel_z:
      name: "MPU6050 Accel Z"
    gyro_x:
      name: "MPU6050 Gyro X"
    gyro_y:
      name: "MPU6050 Gyro Y"
    gyro_z:
      name: "MPU6050 Gyro Z"
    temperature:
      name: "MPU6050 Temperature"
  #    internal: false # publish sensor data to Home Assistant and/or web server

  - platform: bme280_i2c
    update_interval: 10s
    temperature:
      name: "BME280 Temperature"
    pressure:
      name: "BME280 Pressure"
    humidity:
      name: "BME280 Humidity"

  - platform: adc
    pin: GPIO05
    name: VBUS Voltage
    update_interval: 10s
    attenuation: 12dB
    filters:
      - multiply: 8.47742
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

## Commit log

2025-03-27 init project
    [JST SM07B-SRSS-TB.step, JST-PH-2 v1.step, KMS221GPLFS.step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]
2025-03-27 Apply automatic changes
    [cover_with_lcd.stl, esp32stepper-bom.xlsx, metal.step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]
2025-04-03 add license
    [esp32stepper.kicad_pcb, esp32stepper.kicad_sch]

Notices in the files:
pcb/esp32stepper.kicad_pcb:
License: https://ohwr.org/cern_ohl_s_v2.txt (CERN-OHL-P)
